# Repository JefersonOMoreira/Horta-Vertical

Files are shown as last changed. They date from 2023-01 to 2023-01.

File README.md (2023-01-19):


<div align = "justify">

# **Irrigação do Jardim Vertical do Prédio A**

## __Descrição Técnica__
O objetivo do projeto é realizar a irrigação do Jardim Vertical do prédio A com períodos e durações de irrigação pré-estabelecidos, além de possuir acionamento remoto por uma API REST. Os dados de *status* da válvula solenoide serão enviados para a API da plataforma ThingSpeak.

## __Teoria__
### **Protocolo HTTP**
Protocolo de comunicação criado no começo da década de 90 por Tim Berners Lee. Ele permite a distribuição de quaisquer tipos de dados por meio da internet. 
<div align = "center">

</div>

Esse protocolo é unidirecional, com conexão intermitente e composto pelo cliente e pelo servidor. O cliente pode ser um navegador *web*, dispositivo móvel ou qualquer dispositivo conectado à internet. O servidor permite: 
- Armazenamento e o backup de dados;
- Compartilhamento de sistemas;
- Controle de usuários;
- Outros serviços. 

Basicamente, o HTTP é um protocolo de **requisição-resposta** que permite que o cliente **solicite** ou **requisite** (*request*) uma imagem, um vídeo ou qualquer outro tipo de dado por meio de uma URL, então o servidor recebe a URL e envia uma **resposta** (*response*) contendo o conteúdo especificado pelo cliente e/ou um **código** numérico que representa o *status* da **resposta** enviada. Toda essa comunicação é feita por meio do protocolo TCP/IP ou por meio de TLS (dado criptografado) permitindo o tráfego seguro dados, que unido ao HTTP é chamado de HTTPS.

Para definir o tipo de ação que o servidor tomará, o cliente utiliza comandos chamados **métodos** ou **verbos**. Os mais utilizados são:  
- **GET:** Cliente requisita dados para servidor.  
- **POST:** Cliente envia dados ao servidor. 

O protocolo HTTP é simples e extensível, e essas características o tornam muito utilizado em:
- Arquitetura e Desenvolvimento *Web*;
-  Aplicações IoT; 
- Sistemas Embarcados; 
- Repositórios; 
- Plataformas IoT; 
- Outras aplicações.

Existem outros protocolos comunicação baseados em HTTP, como o **REST**. Ele é mais flexível, leve, rápido e sem restrições para o formato de envio das mensagens, porém o desenvolvedor é responsável pela comunicação transparente do protocolo.

### **Solenoide**
Consiste em um eletroimã (dispositivo que converte energia elétrica em energia mecânica), ou seja, uma bobina de núcleo metálico e fios de cobre esmaltados enrolados em espiral.   
O seu princípio de funcionamento básico, é a geração de campo magnético quando há passagem de corrente elétrica pela solenoide. Esse campo magnético cria um movimento linear que permite acionar interruptores, válvulas ou ignição automotiva, automatizando esses e outros processos.
<div align = "center">

</div>

A principal vantagem em relação aos ímãs permanentes, é que os solenoides podem ser desligados com a ausência da corrente. São muito utilizados na área de: Eletrônica Geral, Automação, Sistema Embarcado Automotivo e Aeronaútico, entre outras aplicações. Em nosso projeto será utilizado uma solenoide que permitirá ou não a passagem de água de acordo com a programação do microcontrolador.

### **Capacitor**
Dispositivo eletrônico formado por dois terminais separados por um  material isolante elétrico, ele tem a função de armazenar cargas elétricas e fornecê-las ao circuito.  

<div align = "center">

</div>

São utilizados também para filtrar a corrente elétrica e evitar ruídos vindos de outros componentes, que no caso abaixo, é o ruído presente na Fonte AC/DC do circuito da caixa de passagem.

### **Relé**
Componente eletromecânico composto por uma solenoide e uma mola de rearme conectada à um contato e à dois terminais Normalmente Fechado (**NF**) e Normalmente Aberto (**NA**). O estado de repouso do relé é **NF**.  
Ao energizar o relé, aciona-se a solenoide, ela cria um campo eletromagnético, que por sua vez, atrai o contato e muda sua a posição para o terminal **NA**.  

<div align = "center">

</div> 

Principal vantagem é que devido ao isolamento da solenoide em relação aos contatos, não há mistura de sinais. Esse dispositivo é muito utilizado na área de: Automação, Elétrica, Eletrônica, IoT, entre outras. 

### **Transistor**
Dispositivo semicondutor feito de silício ou germânio que possui três terminais: **emissor**, **base** e **coletor**. Ele foi criado com o intuito de controlar uma corrente maior por meio de uma corrente com a intensidade menor na **base** do transistor, com isso, é possível amplificar ou atenuar a intensidade da corrente ou barrar sua passagem. Outra possibilidade é de funcionar como uma chave, impedindo ou permitindo a passagem de corrente elétrica, desligando ou ligando o transistor, isso também é chamado de **modo de operação**.  

<div align ='center'>

</div>

Para controlar a passagem de corrente elétrica, controla-se a passagem dos elétrons dentro do dispositivo. Com o objetivo de conduzir corrente e aumentar o sinal do transistor, realiza-se a **dopagem**, que é a susbstituição dos átomos de silício ou germânio por outros elementos químicos, isso facilita a passagem de corrente. Existem dois tipo de dopagem: **N** e **P**.  
Na dopagem **tipo N** os átomos adicionam mais elétrons à rede cristalina do transistor. Na dopagem **tipo P** os átomos adicionam menos elétrons à mesma rede criando lacunas, portanto, tendo maior carga positiva. O **modo de operação** dos transistores depende da sua configuração e da **polarização direta** ou **reversa**, isso afeta diretamente espessura da **barreira de potencial** ou **região de depleção**, que é uma barreira formada pela falta ou excesso de elétrons relacionada a força de atração entre eles de acordo com a diferença de potencial. Há três tipos de configurações:
- Transistor "sanduíche" ou diodo;
- Transistor de Bipolar de Junção (TBJ): **tipo** **PNP** e **NPN**;
- Transistor de Efeito de Campo (TEC).

<div align ='center'>

</div>

As suas principais aplicações são: 
- Circuitos integrados; 
- Aparelhos eletrônicos e eletrodomésticos; 
- Portas lógicas;
- Outras aplicações.

### **Diodo**
Dispositivo semicondutor que possui dois terminais ânodo (A) e o cátodo (K). Formado pela junção de dois cristais de germânio ou silício dopados  do **tipo P** e **N**, e além disso, permite a passagem de corrente por um único sentido. Para permitir a passagem de corrente, deve-se primeiramente  **polarizar diretamente** o circuito e depois ultrapassar a **tensão de ruptura** (0,7 V), para impedir a passagem de corrente deve-se **polarizar inversamente**.  
<div align = 'center'>
 
</div>

Devido à existência de vários tipos de diodo (LED e  Diodo Zener) e cada tipo exerce funções específicas, portanto, o diodo pode ter muitas aplicações, como:
- Pontes Retificadoras;
- Iluminação LED;
- Proteção de componentes; 
- Outras aplicações.

### **Microcontrolador**
Microcontrolador é um dispositivo eletrônico que une hardware e software em um Circuito Integrado (CI), basicamente é um microcomputador, ele possui: microprocessador ou CPU, entradas e saídas, porta serial, contadores, temporizadores, circuitos de memória (RAM, Flash e/ou PROM).   

<div align = 'center'>

</div>  

Para funcionar é necessário passar instruções (programar) por meio de Ambiente de Desenvolvimento Integrado (IDE) para que esses comandos sejam convertidos em uma linguagem binária e o microcontrolador entenda, dessa forma, é possível controlar os dispositivos periféricos e receber e/ou enviar dados para partes internas ou para dispositivos externos. O microcontrolador é utilizado em: 
- Produtos eletrônicos e eletrodomésticos;
- Dispositivos de automação; 
- Aplicações IoT;
- Sistemas Embarcados; 
- Sistema de ensino (Arduino); 
- Outros.

### **Fonte AC/DC**
A função desse dispositivo de alimentação é  transformar a tensão que sai da rede elétrica (110 V e 220 V) em uma tensão menor (+3,3V, +5V, +12V e -12V), e que possa ser utilizada por dispositivos eletroeletrônicos e eletrodomésticos, como: *notebook*, *smartphone*, computador, entre outros dispositivos. Tipos básicos são: **fonte linear** e **fonte chaveada**.  

<div align = 'center'>

</div>

Basicamente, na **Fonte Linear**, utiliza-se o transformador para auxiliar na diminuição da tensão alternada da rede elétrica, depois passa por uma série de circuitos que filtram, retificam e regulam a tensão utilizando diodos, capacitores e reguladores de tensão. Ao fim desse processo a tensão é contínua. Já na **Fonte Chaveada**, para que o tamanho dos capacitores e dos transformadores possa ser reduzido, a frequência da tensão da rede é aumentada, depois disso, é realizado o mesmo processo de redução e filtragem da tensão alternada utilizado na **Fonte Linear**.

<div align = 'center'>

</div>

### **Python 3 e Suas Bibliotecas**
[Python 3](https://docs.python.org/3/tutorial/index.html) é uma linguagem de programação [orientada a objetos](https://www.alura.com.br/artigos/poo-programacao-orientada-a-objetos), e utiliza identações para diferenciar seu contexto de execução. Neste projeto, ela foi utilizada para a criação de um script capaz de se inscrever em um tópico MQTT e persistir os dados do tópico em um banco de dados relacional. Neste projeto foram utilizadas algumas bibliotecas do Python3: [paho-mqtt](https://www.eclipse.org/paho/clients/python/docs/), [pymssql](https://pythonhosted.org/pymssql/), [time](https://docs.python.org/3/library/time.html), [datetime](https://docs.python.org/3/library/datetime.html).

### **PI System**
O PI System™ é uma infraestrutura empresarial aberta que conecta dados baseados em sensores, sistemas e pessoas. O resultado é: informações acionáveis e em tempo real que capacitam as empresas a otimizar e transformar seus negócios.

## __Materiais Utilizados__

- 1 NodeMCU ESP8266 v3
- 1 RTC DS1307
- 1 HLK-PM01 AC/DC 220v para 5V
- 6 Conectores Borne KRE 2 Vias
- 5 Resistores 220 ohms 
- 1 Capacitor 100nF
- 1 Diodos 1n4007
- 1 LED verde
- 1 LED vermelho
- 1 LED Azul
- 1 Chave on/off impermeável
- 1 Relé 1 Contato Reversível 5vdc 
- 1 Placa de Fibra de Vidro Virgem Cobreada 10x10 cm
- 1 Plug Conector Metálico Mike Gx16 Para Painel 2 Pinos
- 1 Caixa De Passagem Sobrepor Elétrica 10x15 
- 1 Barramento de pinos (macho)
- 1 Barramento de pinos (fêmea)
- 1 Válvula solenoide 127V 180° (¾ x ¾) VA 04
- 1 Transistor NPN BC547
- 1 Fio com plug de tomada macho
- 1 Porta fusivel
- 1 Fusivel 1A

## __Guia de Instalação__

Configuração da IDE do Arduino para o NodeMCU

Entrar na IDE do Arduino e clicar em Arquivo -> Preferências:  
<div align ='center'>
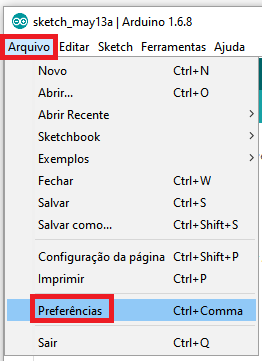
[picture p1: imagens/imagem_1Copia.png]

</div>

Na tela seguinte, copie o link do ESP8266 **http://arduino.esp8266.com/stable/package_esp8266com_index.json** e cole no campo **URLs adicionais de Gerenciadores de Placas**.

A sua tela ficará assim:  

<div align ='center'>  
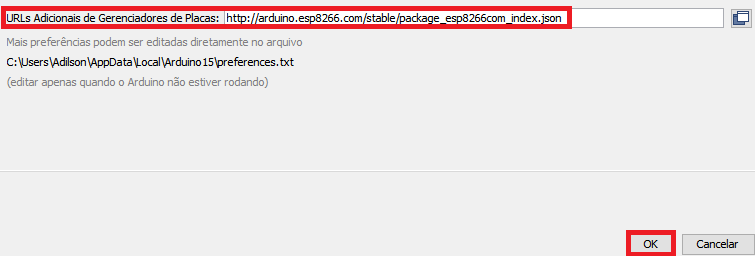
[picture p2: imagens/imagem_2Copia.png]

</div>

Clique em **OK** para retornar à tela principal da IDE.

Agora clique em **Ferramentas** -> **Placa** -> **Gerenciador de Placas**:  

<div align ='center'>  
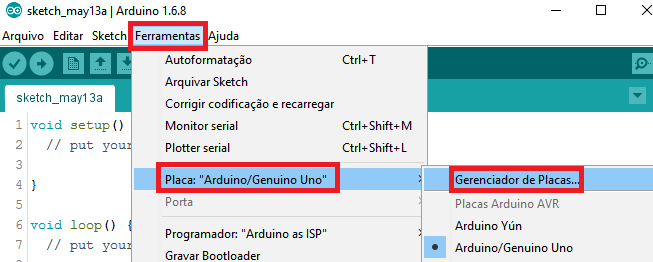
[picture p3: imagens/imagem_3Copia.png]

</div>

Digite ``esp8266``, utilize a barra de rolagem para encontrar o **esp8266 by ESP8266 Community** e clique em **Instalar**

<div align ='center'>  

</div>

Após alguns minutos as placas da linha ESP8266 já estarão disponíveis na lista de placas da IDE do Arduino.

## __Guia de Montagem__

Os componentes devem ser montados da seguinte forma:  

<div align ='center'> 
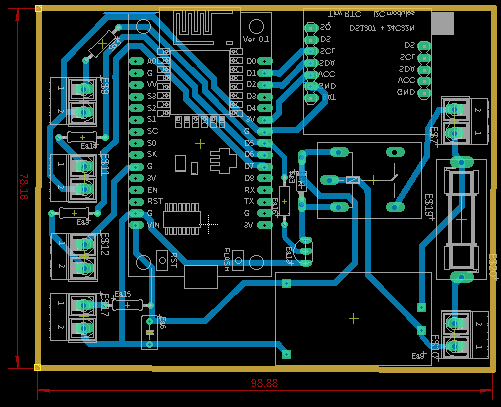
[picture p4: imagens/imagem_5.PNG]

</div>

## __Guia de Implementação__

A válvula solenoide deve ser montada o mais profundo possível dentro da caixa de passagem, senão a tampa não fechará, além disso, deve ficar o mais próximo das extremidades da caixa de pssagem para que não atrapalhe a montagem da parte eletrônica.
No caso de vazamentos, para evitar possíveis danos na parte eletrônica da caixa de passagem, separou-se a parte que contém a válvula solenoide da parte eletrônica, criando-se uma divisória de acrílico e silicone, como mostra a imagem abaixo.
<div align ='center'> 
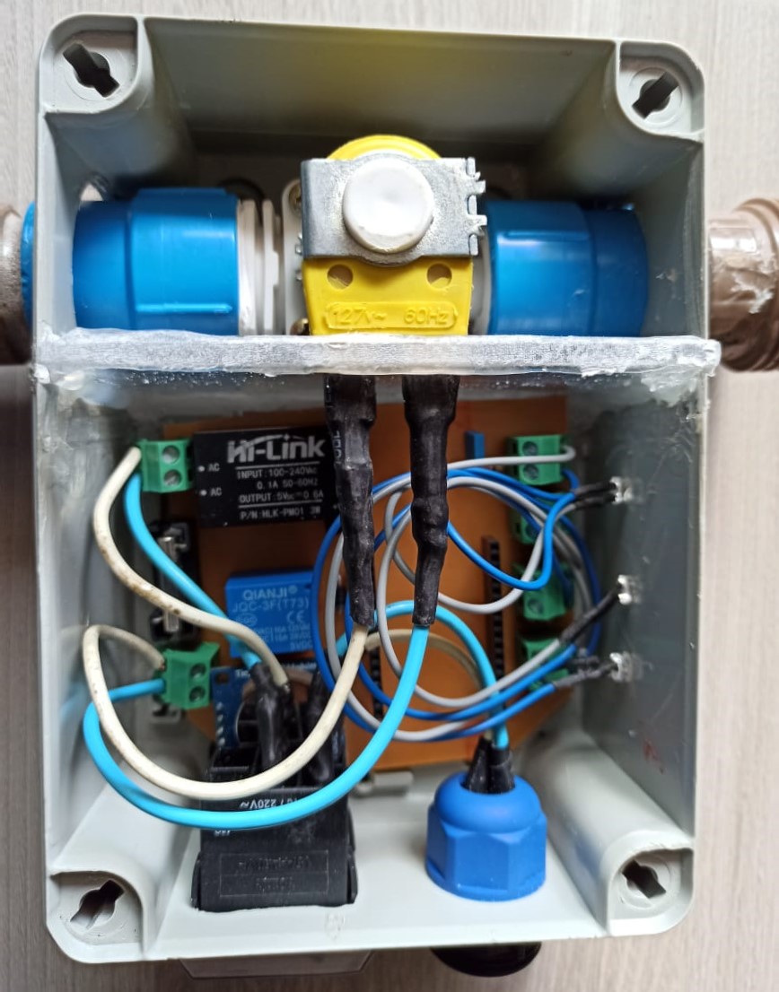
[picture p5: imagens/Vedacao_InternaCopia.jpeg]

</div> 

Além disso, foi deixada uma abertura em torno do cano, na parte da válvula solenoide, para que haja o escoamento da água em caso de vazamento.   
<div align ='center'> 
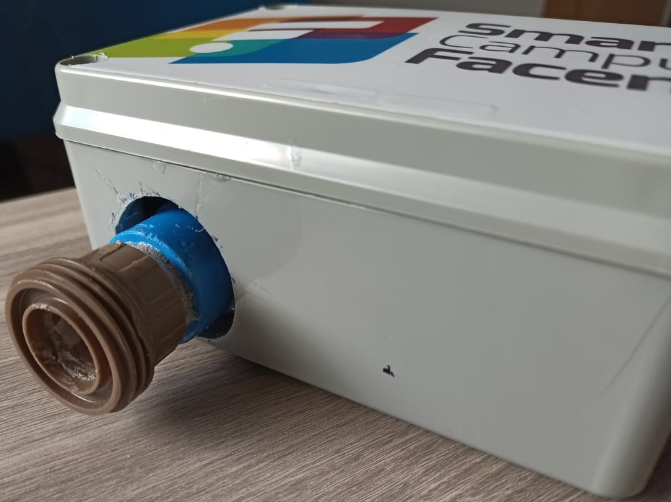
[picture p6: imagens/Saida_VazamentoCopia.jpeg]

</div>

O botão ON/OFF e o *plug* de alimentação devem ficar suficientemente altos para que a placa que contém o circuito possa se acomodar em baixo deles, como mostram as imagens anteriores.  
<div align ='center'> 
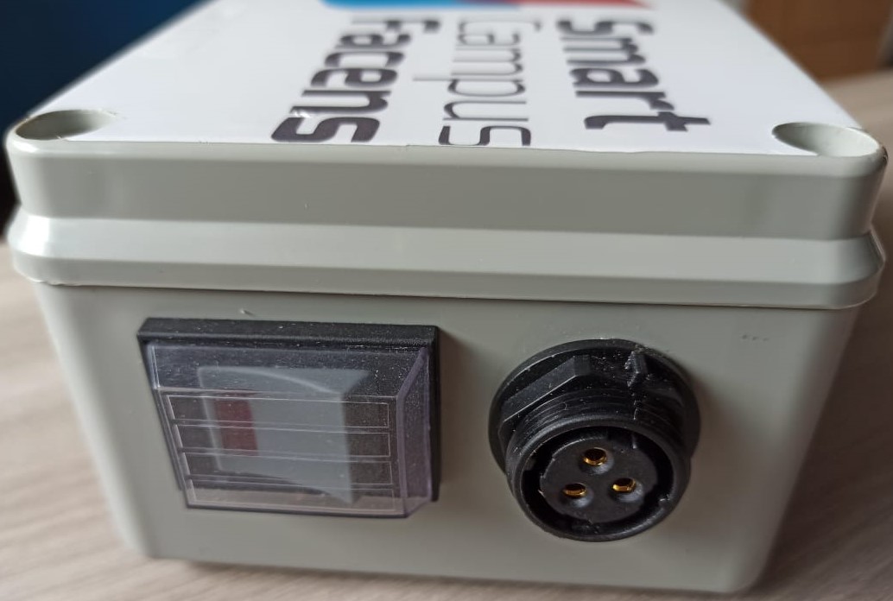
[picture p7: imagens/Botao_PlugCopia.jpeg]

</div>

Para evitar que a água da irrigação ou a água de eventuais chuvas cheguem à parte eletrônica, a
parte superior da caixa de passagem deve ser completamente vedada. Na imagem a seguir, também foram vedados: 
- O cano de passagem da água;
- Os LEDs indicadores de:
    - Alimentação;
    - Envio de dados para API;
    - Acionamento da solenoide para irrigação.  

<div align ='center'> 
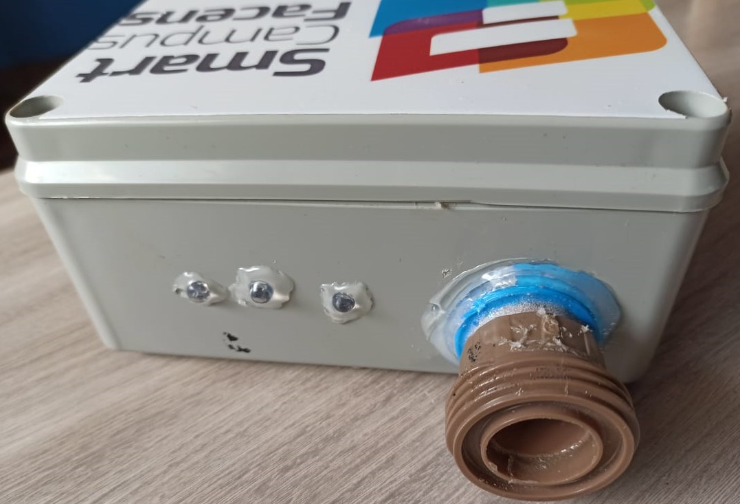
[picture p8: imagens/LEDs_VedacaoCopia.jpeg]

</div> 

No caso de haver necessidade de remoção da caixa de passagem, foram implementados registros para garantir a segurança do aparelho e a continuidade da irrigação de forma manual.    
<div align ='center'> 
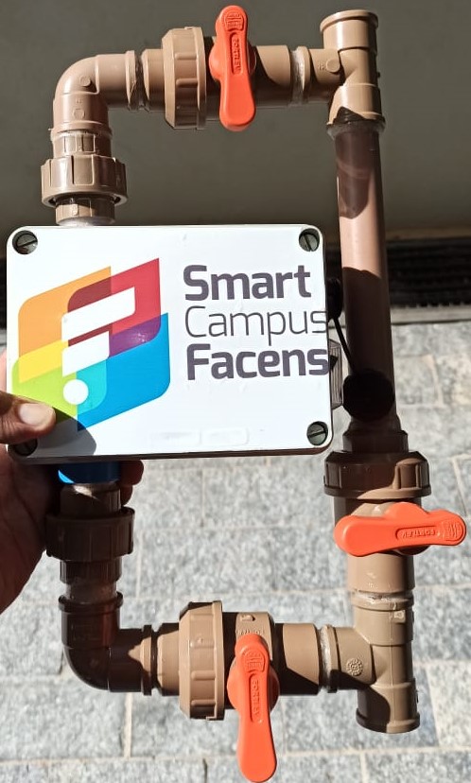
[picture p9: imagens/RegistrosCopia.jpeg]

</div>

### **Banco de dados**

Foi criado uma tabela chamada **jd_Vertical_PredioA** no *database* **clima** com os seguintes atributos:
- **data** - data e hora que a mensagem foi enviada.
- **v1** - status da válvula de irrigação.

Estrutura da tabela:



Dados apresentados na tabela:

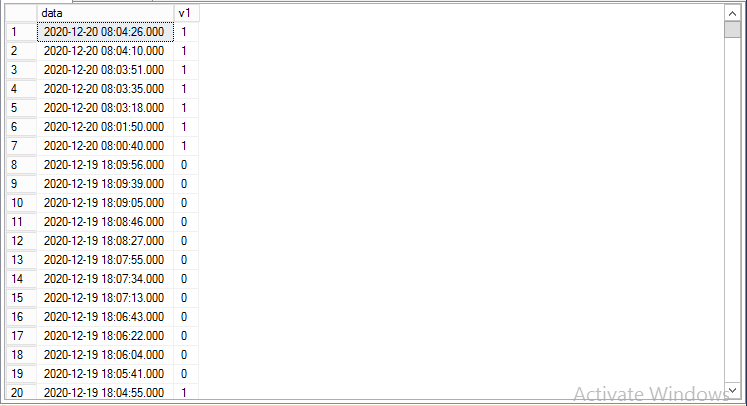
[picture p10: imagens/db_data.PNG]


### **PI Data Archive**

Foram criadas 2 *tags* para armazenar as informações de cada atributo no *Data Archive*.

*Tags* criadas para armazenar informações do Jardim Vertical do Prédio A:



Tags com o modelo de consulta SQL:

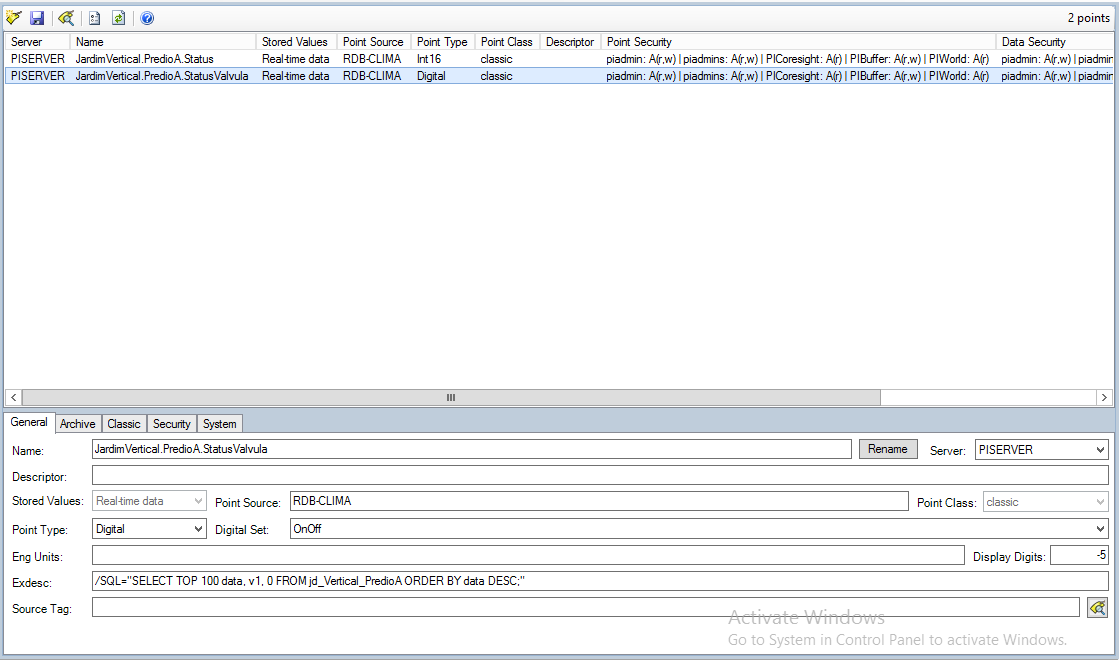
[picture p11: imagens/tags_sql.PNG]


A tag **JardimVertical.PredioA.StatusValvula** consulta os dados no SQL Server, já a tag **JardimVertical.PredioA.Status** armazena dados vindos de análises do PI Server.

### **Jardim Vertical do Prédio A Template**
Foi criado um template para organizar os elementos. Foram adicionadas todas as tags com um caminho genérico **\\%Server%\%..\Element%.%Element%.%Attribute%**, que por sua vez busca a *tag* de acordo com o diretório gerado pelos nomes dos elementos.

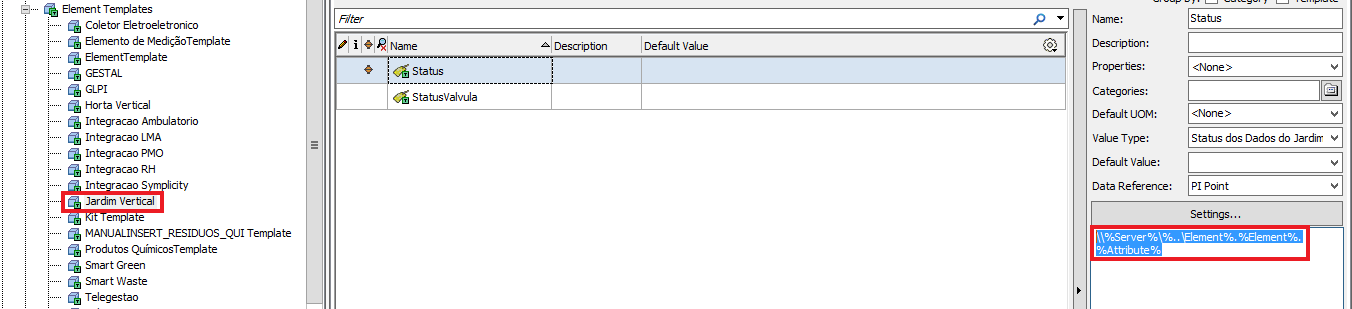
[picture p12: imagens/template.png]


O template também contém análises para indicar se os dados estão atualizados e disparar emails caso não esteja.

Análise do status da válvula
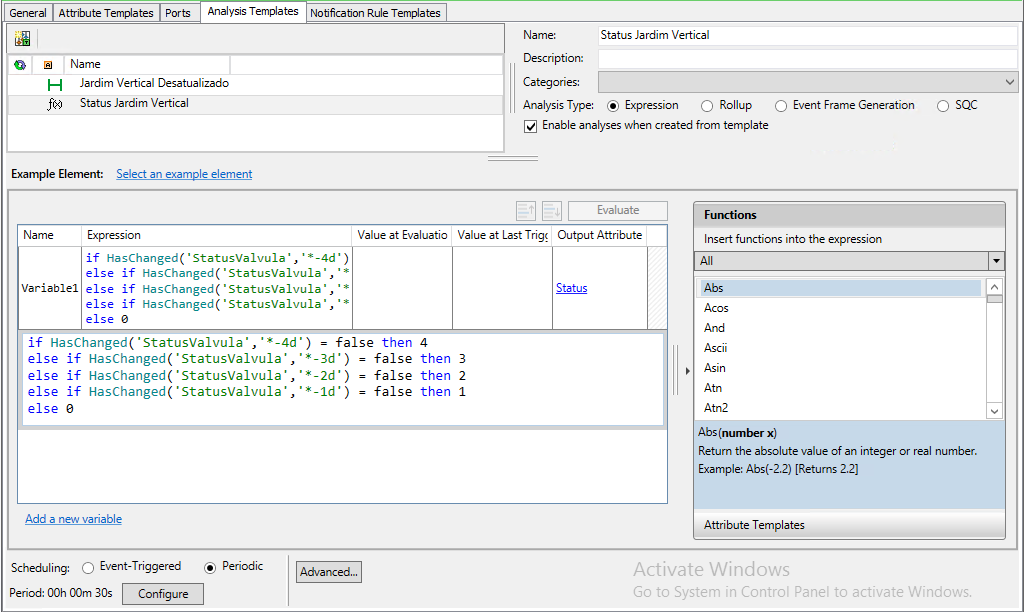
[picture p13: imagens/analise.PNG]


Análise para envio de email
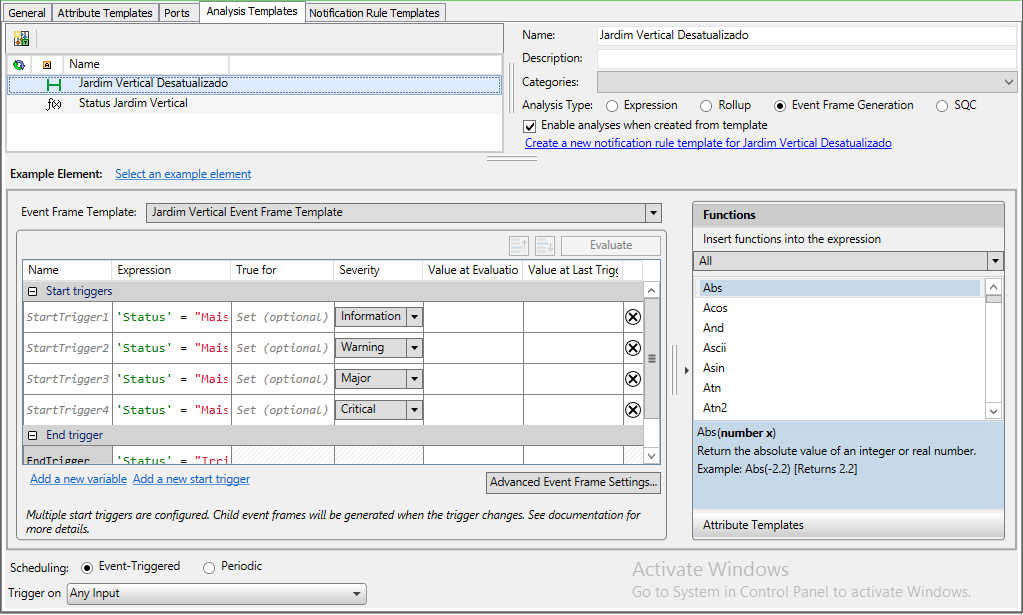
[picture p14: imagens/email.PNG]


### **Jardim Vertical do Prédio A Enumeration Sets**
Foram utilizados *enumeration sets* para transformar os números inteiros vindo das análises em frases para a melhor clareza das informações.
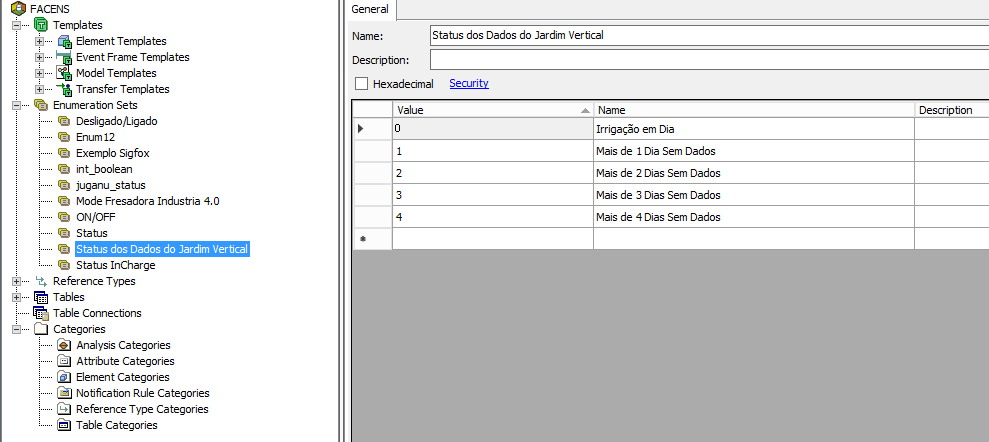
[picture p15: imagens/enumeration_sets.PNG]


### **Elements**
A árvore de elementos foi criada de forma a trabalhar em conjunto com o template formando o caminho das *tags*.

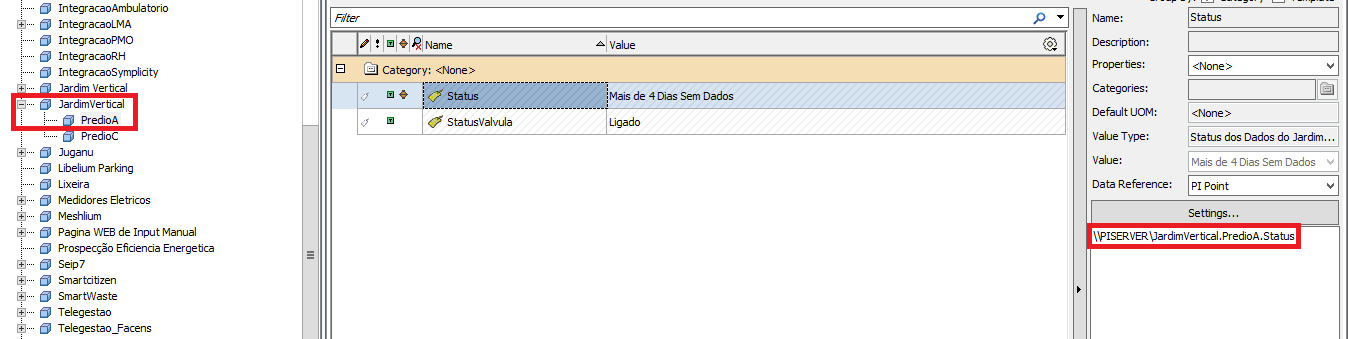
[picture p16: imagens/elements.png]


### **Script usando Python3**

Foi criado um [*script*](https://gitlab.com/smart-campus-facens/irrigacao-jardim-vertical-predio-a/-/blob/master/Jardim%20Vertical%20Predio%20A%20-%20Scripts/Pegar%20Dados%20da%20API%20e%20P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) em *python* o qual realiza *requests* na API *Rest* do Thingspeak e salva suas mensagens na tabela do banco de dados criada acima.

### **Servidor**

Ubuntu 16.04.7 LTS

O [*script*](https://gitlab.com/smart-campus-facens/irrigacao-jardim-vertical-predio-a/-/blob/master/Jardim%20Vertical%20Predio%20A%20-%20Scripts/Pegar%20Dados%20da%20API%20e%20P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) criado está no seguinte caminho do servidor:

/srv/jobs/smartcontrol/jardimvertical

Foi criado um arquivo .sh para que o [*script*](https://gitlab.com/smart-campus-facens/irrigacao-jardim-vertical-predio-a/-/blob/master/Jardim%20Vertical%20Predio%20A%20-%20Scripts/Pegar%20Dados%20da%20API%20e%20P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) fosse executado no *crontab*. O conteúdo do arquivo é o seguinte:

```
#!/bin/bash

cd /srv/jobs/smartcontrol/jardimvertical

python3 apiJARDIMVERTICAL_Predio_A.py

cd -

```

Em /etc/crontab foi aicionado o caminho do arquivo .sh criado acima com seu respectivo período de execução.

Imagem do crontab:

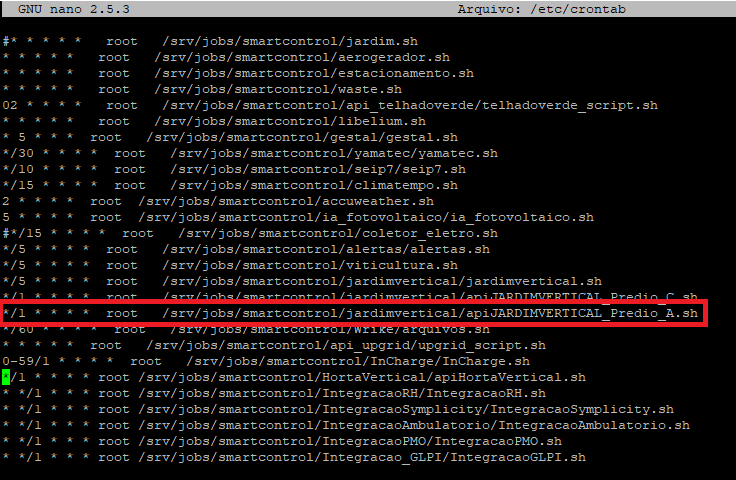
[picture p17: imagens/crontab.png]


## __Visualização criada no projeto__

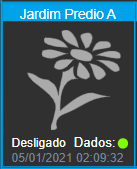
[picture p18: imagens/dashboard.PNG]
 

## __Resultados Esperados__
O equipamento deve realizar a irrigação nos horários programados e durante esse período deve enviar seu *status* para os canais de recebimento de dados da API (*endpoints*). Além disso, o equipamento deve responder aos acionamentos remotos enviados pela API.

## __Pontos de Atenção__
 
Para evitar que a irrigação continue acionada o tempo todo, atente-se para que o acionamento remoto via API não fique acionado.

Para que tudo se encaixe perfeitamente, atente-se aos processos de montagem ditos anteriormente no **Guia de Implementação**, pois não há folgas para a montagem dentro do espaço da caixa de passagem.

## __Referências__
**Sites**:  
[Alura](https://www.alura.com.br/artigos/qual-e-diferenca-entre-http-e-https "HTTP")  
[Athos Eletronics](https://athoselectronics.com/rele/ "Relé")   
[Athos Eletronics](https://athoselectronics.com/diodo/ "Diodo")  
[Brasil Escola](https://brasilescola.uol.com.br/fisica/transistor.htm "Transistor e Diodo")  
[Brasil Escola](https://brasilescola.uol.com.br/fisica/capacitores.htm "Capacitor")  
[Clube do Hardware](https://www.clubedohardware.com.br/artigos/energia/tudo-o-que-voc%C3%AA-precisa-saber-sobre-fontes-de-alimenta%C3%A7%C3%A3o-r34441/ "Fonte AC/DC")  
[Detto](https://detto.com.br/para-que-serve-um-servidor/ "HTTP")  
[Developer Mozilla](https://developer.mozilla.org/pt-BR/docs/Web/HTTP/Overview "HTTP")  
[Eletron Jun](https://www.eletronjun.com.br/post/o-que-s%C3%A3o-microcontroladores-descubra-suas-aplica%C3%A7%C3%B5es "Microcontrolador")  
[Ilumisul](http://www.ilumisul.com.br/como-funciona-um-solenoide/ "Solenoide")  
[Medium](https://medium.com/@renancprata/mqtt-vs-rest-perspectiva-de-uma-implementa%C3%A7%C3%A3o-iot-4c7e1f26689c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,instantaneamente%2C%20conforme%20esperado%20pelos%20clientes. "HTTP")  
[Mundo da Elétrica](https://www.mundodaeletrica.com.br/o-que-e-rele-como-funciona-um-rele/ "Relé")  
[Stack Overflow](console.thinger.io/#!/console/devices "REST e HTTP")  
[Treina Web](https://www.treinaweb.com.br/blog/o-que-e-http-request-get-post-response-200-404/ "HTTP")  
[Wikipédia](https://pt.wikipedia.org/wiki/Hypertext_Transfer_Protocol "HTTP")  
[Wikipédia](https://pt.wikipedia.org/wiki/Microcontrolador "Microcontrolador")  

**Canais:**  
[WR Kits](https://www.youtube.com/watch?v=jt1gBC2Bo7g "Transistor")

</div>

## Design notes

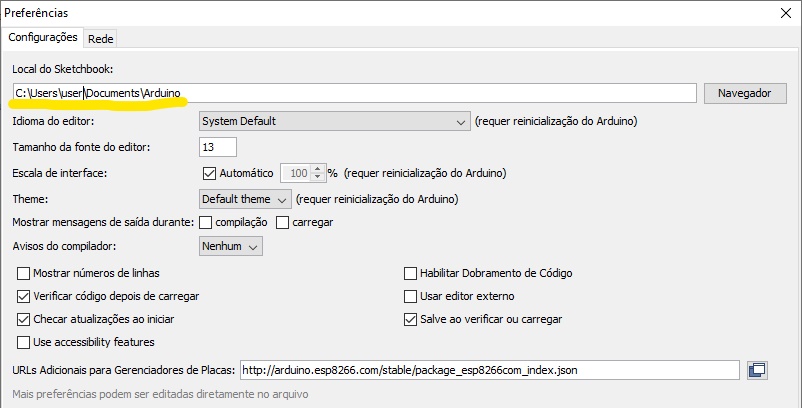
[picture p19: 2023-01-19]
imagens/diretorioArduino.jpg

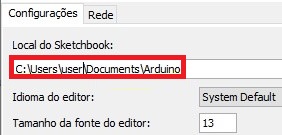
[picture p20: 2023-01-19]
imagens/diretorioArduinoCopia.jpg

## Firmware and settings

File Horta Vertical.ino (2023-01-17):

/*
  O sistema é ligado para efetuar a irrigação e enquanto esta ligado fica mandando o status da valvula. Apos desligar passa mais 5 minutos enviando o status da valvula desligada
*/
#include <ArduinoJson.h> // Versão 5.12.0
#include <ESP8266WiFi.h>
#include <ESP8266HTTPClient.h>
#include <Wire.h>       //I2C library
#include <RtcDS3231.h>  //RTC library
#include <EEPROM.h>
#include <ESP8266mDNS.h>
#include <WiFiUdp.h>
#include <ArduinoOTA.h>

WiFiClient client;

// ============================================== RTC setup ================================================================================
RtcDS3231<TwoWire> rtcObject(Wire); //Uncomment for version 2.0.0 of the rtc library
HTTPClient http;

#define rele 14
#define ledEnvio 12

String payloadGlobal; //Essa variavel foi criada para conseguirmos acessar a variavel payload de qualquer lugar do codigo
int horas;
int minutos;
int v1;
int contador = 0;
String acessoRemoto = "0"; //Trocar acesso remoto por status somente
String acessoLocal = "0";


const char* ssid = "########";
const char* password = "########";

void setup () {
  //================ Setup WIFI
  Serial.begin(115200); 
  WiFi.begin(ssid, password); // Inicia o wifi com as credenciais passadas acima

  //================ Tenta se conectar ao WIFI 60 vezes senão conectar inicia sem conexão com o WIFI
  while (WiFi.status() != WL_CONNECTED && contador < 60) {
    delay(1000);
    Serial.print("Connecting..");
    contador ++;
  }
  if (WiFi.status() == WL_CONNECTED) {
    Serial.print("Conectado");
  } else {
    Serial.print("Iniciando sem conexão com WIFI");
  }
  //================ Setup RTC =========================
  Serial.begin(115200);  //Starts serial connection
  rtcObject.Begin();     //Starts I2C
  //RtcDateTime currentTime = RtcDateTime(2020, 07, 06, 10, 24, 10); //define date and time object
  //rtcObject.SetDateTime(currentTime); //configure the RTC with object
  
  //==================================================================================================== Setup OTA ======

  // Port defaults to 8266
  // ArduinoOTA.setPort(8266);

  // Hostname defaults to esp8266-[ChipID]
  ArduinoOTA.setHostname("Jardim Vertical Predio K V1");

  // No authentication by default
  // ArduinoOTA.setPassword((const char *)"Smart2017!");

  ArduinoOTA.onStart([]() {
    Serial.println("Start");
  });
  ArduinoOTA.onEnd([]() {
    Serial.println("\nEnd");
  });
  ArduinoOTA.onProgress([](unsigned int progress, unsigned int total) {
    Serial.printf("Progress: %u%%\r", (progress / (total / 100)));
  });
  ArduinoOTA.onError([](ota_error_t error) {
    Serial.printf("Error[%u]: ", error);
    if (error == OTA_AUTH_ERROR) Serial.println("Auth Failed");
    else if (error == OTA_BEGIN_ERROR) Serial.println("Begin Failed");
    else if (error == OTA_CONNECT_ERROR) Serial.println("Connect Failed");
    else if (error == OTA_RECEIVE_ERROR) Serial.println("Receive Failed");
    else if (error == OTA_END_ERROR) Serial.println("End Failed");
  });
  ArduinoOTA.begin();
  Serial.println("Ready");
  Serial.print("IP address: ");
  Serial.println(WiFi.localIP());

  //==================================================================================================== Setup Entradas e Saidas =======
  pinMode(ledEnvio, OUTPUT);
  pinMode(rele, OUTPUT);

  //==================================================================================================== Setup EEPROM =================
  EEPROM.begin(4);
  if(!EEPROM.read(0)&&!EEPROM.read(1)){
  EEPROM.write(0, 10);
  EEPROM.write(1, 11);
  EEPROM.commit();
  }

  Serial.print("Time0 EEPROM: ");
  Serial.println(EEPROM.read(0));

  Serial.print("Time1 EEPROM: ");
  Serial.println(EEPROM.read(1));
  atualizaHora();

}

void loop() {

  ConsultaHoraAtualRTC();
  Serial.println();
  Serial.print("Payload:");
  Serial.println(payloadGlobal);
  Serial.print("Acesso Remoto:");
  Serial.println(acessoRemoto);
   
  //Executa as funçoes que dependem de internet
  if (WiFi.status() == WL_CONNECTED) {
    ConsultaStatusBotaoAPI();
    ConsultaProgramacaoServidor();
    //Atualiza o RTC com horario do servidor a cada hora
    if (minutos == 0) atualizaHora();
  }
  
  // Se houver acionamento manual ou estiver no horario de ligar realiza a irrigação
  if (horas == 7 && minutos < EEPROM.read(0) || (acessoRemoto != payloadGlobal && payloadGlobal == "1") || horas == 16 && minutos < EEPROM.read(1)) {
    digitalWrite(rele, HIGH);
    v1 = 1;
    EnviaStatusValvulaAPI(); // Envia o status da valvula para o Thingspeak
    acessoRemoto = payloadGlobal; // Em caso de acesso manual garante que sera enviado apenas uma vez o status para o servidor
  } 
  // Se houver o desacionamento manual ou estiver no horario de desligar realiza a paralização da irrigação
  else if (horas == 7 && minutos >= EEPROM.read(0) && minutos < EEPROM.read(0) + 5 || (acessoRemoto != payloadGlobal && payloadGlobal == "0" ) || horas == 16 && minutos >= EEPROM.read(1) && minutos < EEPROM.read(1) + 5) {
    digitalWrite(rele, LOW);
    v1 = 0;
    EnviaStatusValvulaAPI(); // Envia o status da valvula para o Thingspeak
    acessoRemoto = payloadGlobal; // Em caso de acesso manual garante que sera enviado apenas uma vez o status para o servidor
  }

  //==================================================================================================== Caso perca a conexão ele tenta reconectar de novo
  if (WiFi.status() != WL_CONNECTED) {
    WiFi.begin(ssid, password);
    contador = 0;
    while (WiFi.status() != WL_CONNECTED && contador < 15) {
      delay(1000);
      Serial.print("Tentando Reconexão...");
      contador ++;
    }
  }
ArduinoOTA.handle();
}


//==================================================================================================== Pega Dado do fild1 do Thingspeak
void ConsultaStatusBotaoAPI() {
  if (WiFi.status() == WL_CONNECTED) { //Check WiFi connection status
    HTTPClient http;  //Declare an object of class HTTPClient

    http.begin(client, "##########################################"); //Specify request destination
    int httpCode = http.GET();                                                              //Send the request

    if (httpCode > 0) { //Check the returning code
      //########################################################################

      //========================================================================
      // Link para gerar o parsing Json: https://arduinojson.org/v5/assistant/
      //========================================================================

      //########################################################################

      //========================================================================
      // Exemplo de consulta de um field do projto Automação do Jardim Vertical
      //========================================================================

      const size_t capacity = JSON_ARRAY_SIZE(1) + JSON_OBJECT_SIZE(2) + JSON_OBJECT_SIZE(10) + JSON_OBJECT_SIZE(15) + 470;
      // DynamicJsonBuffer jsonBuffer(capacity);

      DynamicJsonDocument doc(capacity);

      //JsonObject& root = jsonBuffer.parseObject(http.getString());
      String jsonReturn = http.getString();
      deserializeJson(doc, jsonReturn);
      //feeds_0 = doc["feeds"][0];

      const char* payload = doc["feeds"][0]["field1"]; //Variavel global por isso nao tem "return"
      Serial.print("Status Botao API: ");
      payloadGlobal = payload;
      Serial.println(payloadGlobal);
    }

    http.end();   //Close connection
  }


}

//==================================================================================================== Pega hora e minuto do RTC
void ConsultaHoraAtualRTC() {

  RtcDateTime currentTime = rtcObject.GetDateTime();    //get the time from the RTC
  horas = currentTime.Hour();  //Variavel global por isso nao tem "return"
  minutos = currentTime.Minute(); //Variavel global por isso nao tem "return"
  Serial.print("Horario:");
  Serial.print(horas);
  Serial.print(":");
  Serial.println(minutos);
}

// ============================================================================ Consulta o tempo que o a solenoide ficara acionada
void ConsultaProgramacaoServidor() {

  String request_string = "##############################";
  if (client.connect("#############", 80)) {
    http.begin(client, request_string);
    int httpCode = http.GET();

    if (httpCode < 0) {
      Serial.println("request error - " + httpCode);
      return ;
    }
    if (httpCode != HTTP_CODE_OK) {
      Serial.println("Code Error " + httpCode);
      return;
    }
    jsonReturn = http.getString(); //Retorna o json
    Serial.println(jsonReturn);
    DynamicJsonDocument doc(1024);
    deserializeJson(doc, jsonReturn);
    http.end();
    int time0 = (int)doc["time0"];
    int time1 = (int)doc["time1"];
    if (EEPROM.read(0) != time0) {
      EEPROM.write(0, time0);
      EEPROM.commit();
      Serial.println("endereco 0 atualizado");
    }
    if (EEPROM.read(1) != time1) {
      EEPROM.write(1, time1);
      EEPROM.commit();
      Serial.println("endereco 1 atualizado");
    }

    Serial.print("Time0: ");
    Serial.println(time0);
    Serial.print("Time1: ");
    Serial.println(time1);
    delay(1000);
  }
}

//==================================================================================================== Envia status da valvula para o thingspeak
void EnviaStatusValvulaAPI() {

  if (WiFi.status() == WL_CONNECTED) { //Check WiFi connection status
    
    HTTPClient http;  //Declare an object of class HTTPClient
  
    Serial.println("");
    Serial.println("Enviando status para o Thingspeak");
    
    String request_string;
    if (client.connect("###########", 80)) {
  
      if (v1 == 1) {
        request_string = "###########################";
      } else if (v1 == 0) {
        request_string = "##############################";
      }
  
      http.begin(client, request_string);
  
      Serial.println(http.GET());
      
      digitalWrite(ledEnvio, HIGH); //
      delay (1000);                // Acionamento do led de indentificação de envio
      digitalWrite(ledEnvio, LOW); //
  
      http.GET();
      http.end();
    }
  
  }

}

void atualizaHora()
{
  //RtcDateTime currentTime = RtcDateTime(19, 07, 18, 13, 20, 10);

  String request_string = "#################";
  String jsonReturn;
  if (client.connect("###########", 80)) {
    http.begin(client, request_string);
    int httpCode = http.GET();

    if (httpCode < 0) {
      Serial.println("request error - " + httpCode);
      return ;
    }
    if (httpCode != HTTP_CODE_OK) {
      Serial.println("Code Error " + httpCode);
      return;
    }
    jsonReturn = http.getString(); //Retorna o json
    Serial.println(jsonReturn);
    DynamicJsonDocument doc(1024);
    deserializeJson(doc, jsonReturn);
    http.end();
    int dia = (int)doc["dia"];
    int mes = (int)doc["mes"];
    int ano = (int)doc["ano"];
    int hora = (int)doc["hora"];
    int minuto = (int)doc["minuto"];
    int segundo = (int)doc["segundo"];
    //RtcDateTime currentTime = RtcDateTime(19, 07, 18, 13, 20, 10);
    RtcDateTime currentTime = RtcDateTime(ano, mes, dia, hora, minuto, segundo);
    rtcObject.SetDateTime(currentTime);
    Serial.print("Data Servidor: ");
    Serial.print(dia);
    Serial.print("/");
    Serial.print(mes);
    Serial.print("/");
    Serial.println(ano);
    Serial.print(" Hora Servidor: ");
    Serial.print(hora);
    Serial.print(":");
    Serial.print(minuto);
    Serial.print(":");
    Serial.print(segundo);
    delay(1000);
  }

}
